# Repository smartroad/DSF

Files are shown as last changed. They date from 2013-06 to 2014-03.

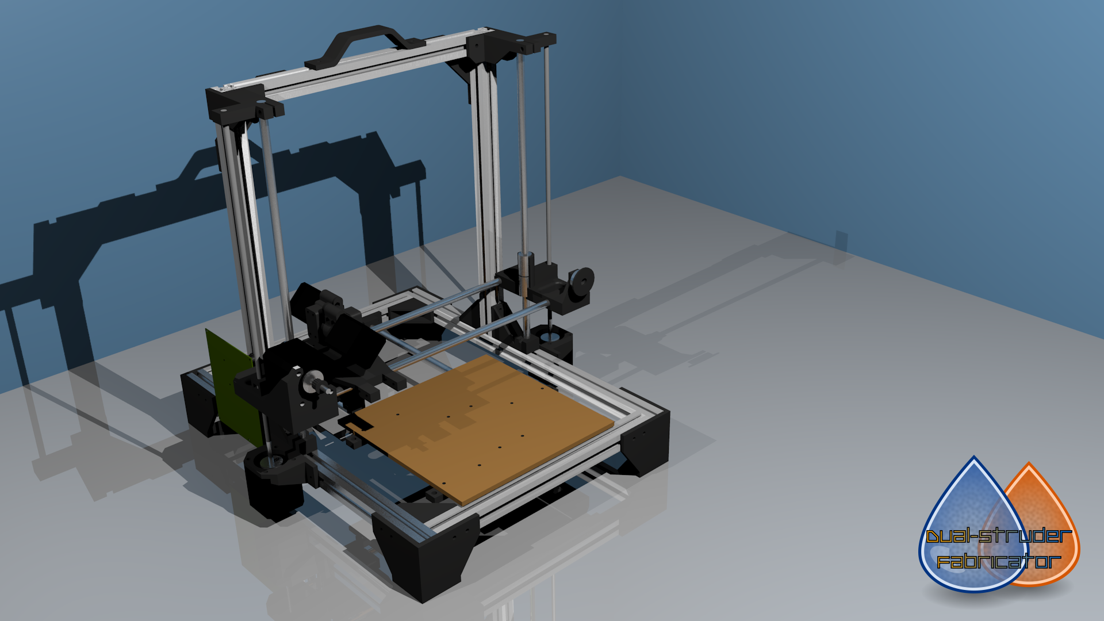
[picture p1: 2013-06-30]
Render.png

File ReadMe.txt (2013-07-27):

For some time I have wanted to design my own printer. Partly so that it will be able to do what I want and secondly for the challenge. Obviously it is much easier these days given the number of designs out there. For my design I had several things that it must be capable of:

1) More than one extruder
2) Use as many of the same vitamins as possible
3) Be simple to construct with the minimum of tools
4) Use as many printable parts as possible
5) No Bowden tube

Now I am not above thinking that some of those ideals may have to be altered but so far, in the planning stage, I think I have hit all of them.

So taking each point in turn:

It currently has space for two extruders – I wanted at least two so that I can leverage Slic3r’s ability to have one extruder for the shell and another for infill. That way I can use Faberdashery’s great colours for the shell and a cheap bulk black or white for the infill. The current extruder/hotend design means that only around 50mm of Y axis is lost when using both extruders.

Each axis uses the same linear bearings, all the printed framework attaches using M4 bolts, bearings used in the belt idlers as used in the extruders and so on. I want to not have a BoM as long as your arm and be able to order from only a few places. Personally I think this is the ideal that will change as the build progresses.

The tools that I think will be needed are screwdrivers, allen (hex) key, wire cutters and a wrench. Again this will probably change as the build progresses.

All structural support parts are printed, only the obvious items aren’t (frame, smooth rods, threaded rod etc).

No Bowden tube for the extruders are used. The current design is for a direct drive extruder – the hobbed bolt is directly attached to the stepper – which reduces the size of the extruder and the need for large printed gears. The actual reason for no Bowden tubes is purely down to I want to print flex-polyester and I haven’t been able to get it to work through my current Huxley’s Bowden. I am considering having one direct drive extruder and maybe replace the second with a Bowden system to reduce carriage weight. This would also allow for another hotend to be potentially added.

Mechanical test video is available: http://youtu.be/PYqmosbdoSI

Build log on my blog: http://fabing3d.wordpress.com/category/dsf/

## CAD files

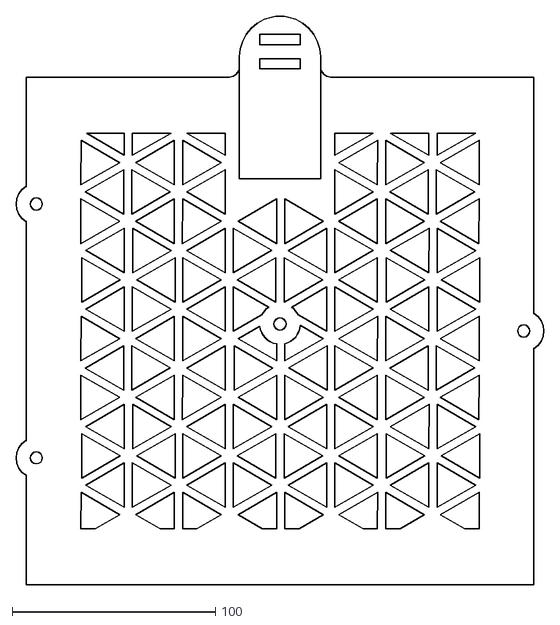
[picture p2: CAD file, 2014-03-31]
DWG/235mm Bed Carrier.dxf
260.0 x 280.0

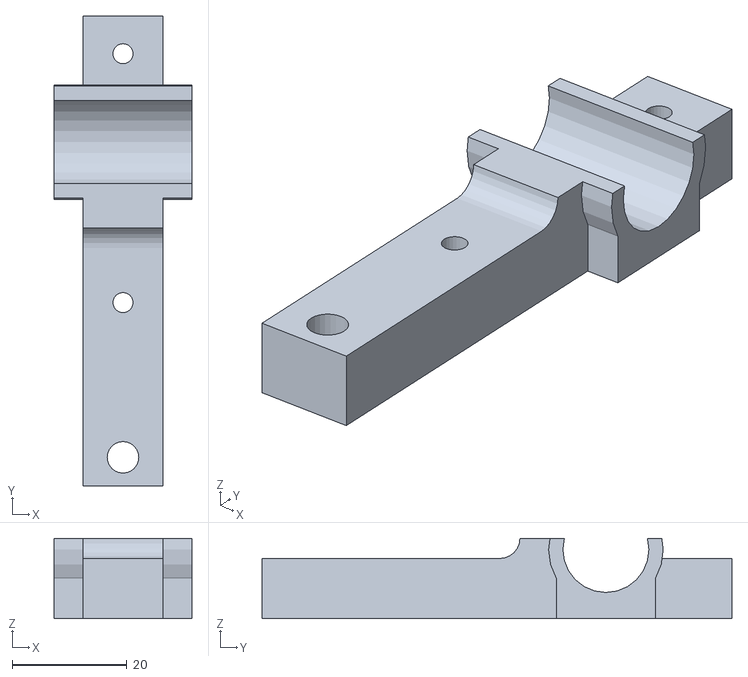
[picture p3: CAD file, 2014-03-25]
STLs/Y Axis Bed Runner Longer x3.stl
24.0 x 82.0 x 14.0

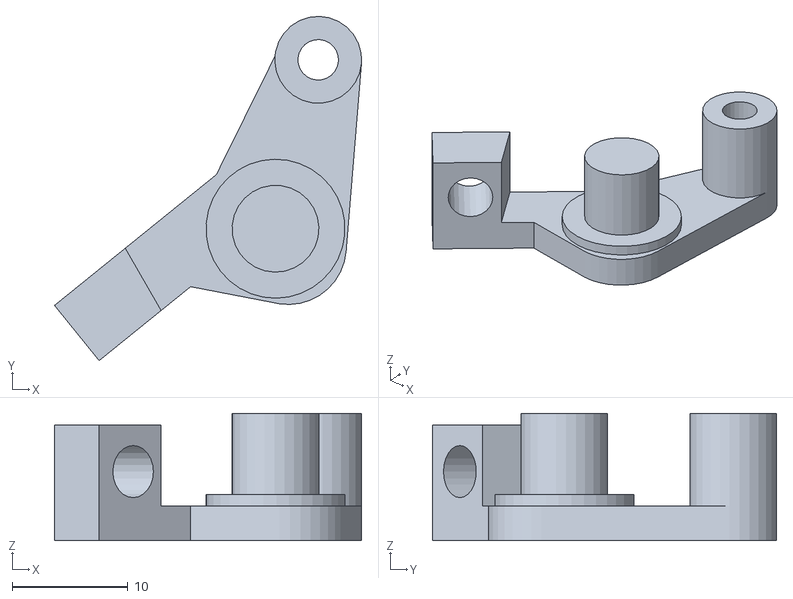
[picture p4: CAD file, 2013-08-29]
STLs/Extruder Arm.stl
26.5 x 29.7 x 11.0

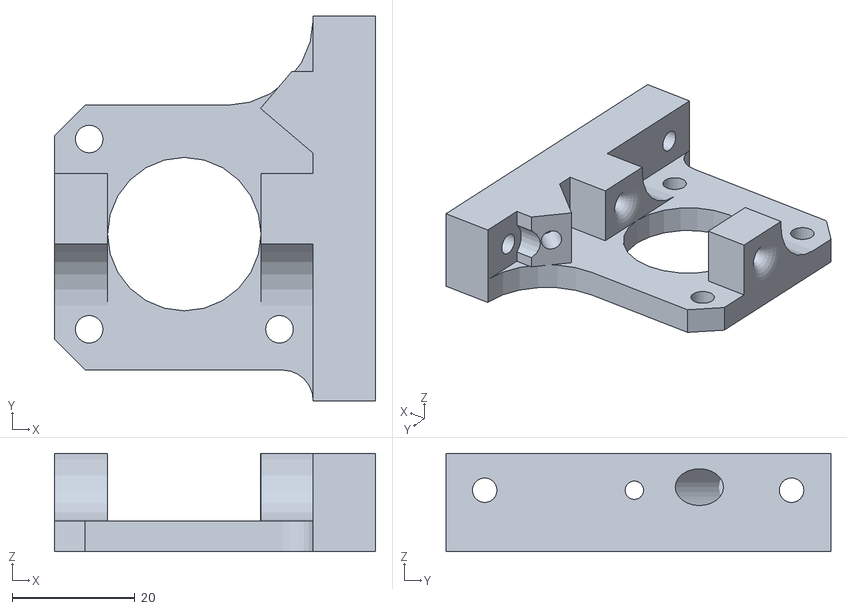
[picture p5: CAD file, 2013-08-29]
STLs/1.75mm Extruder Mount.stl
52.3 x 62.7 x 16.0

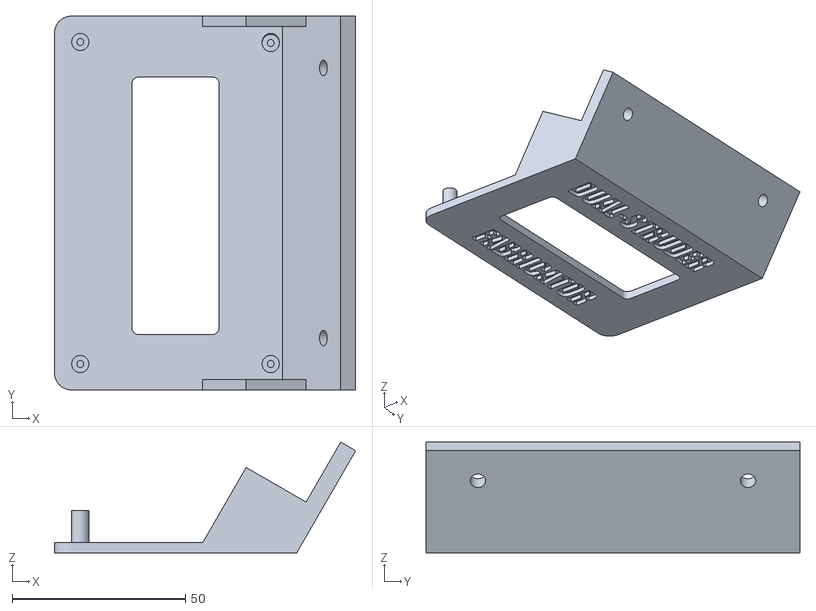
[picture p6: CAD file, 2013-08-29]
STLs/20x4 LCD Mount.stl
87.0 x 108.0 x 32.0

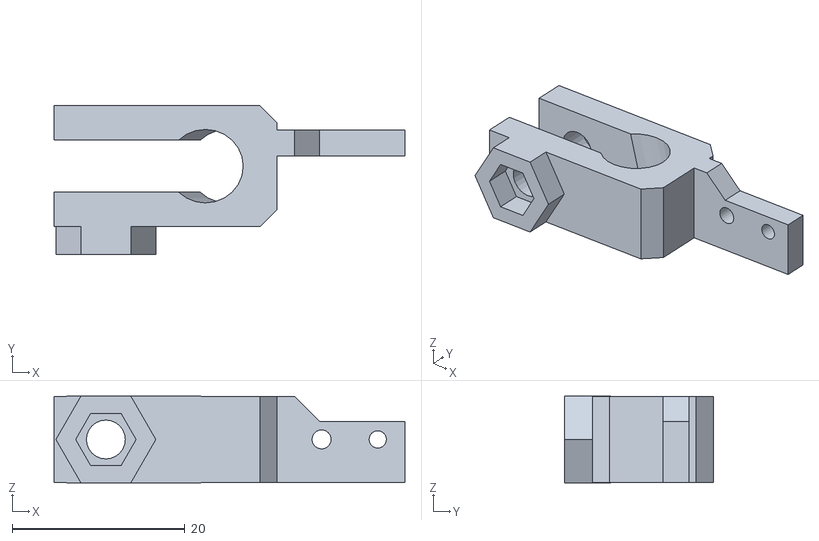
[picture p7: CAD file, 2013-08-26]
STLs/X Axis End Stop.stl
40.6 x 17.2 x 10.0

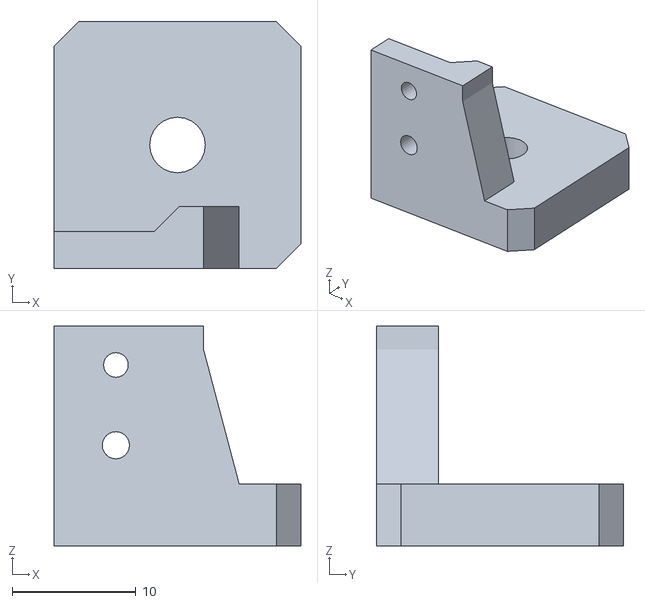
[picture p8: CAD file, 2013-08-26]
STLs/Z Axis End Stop.stl
20.0 x 20.0 x 17.8

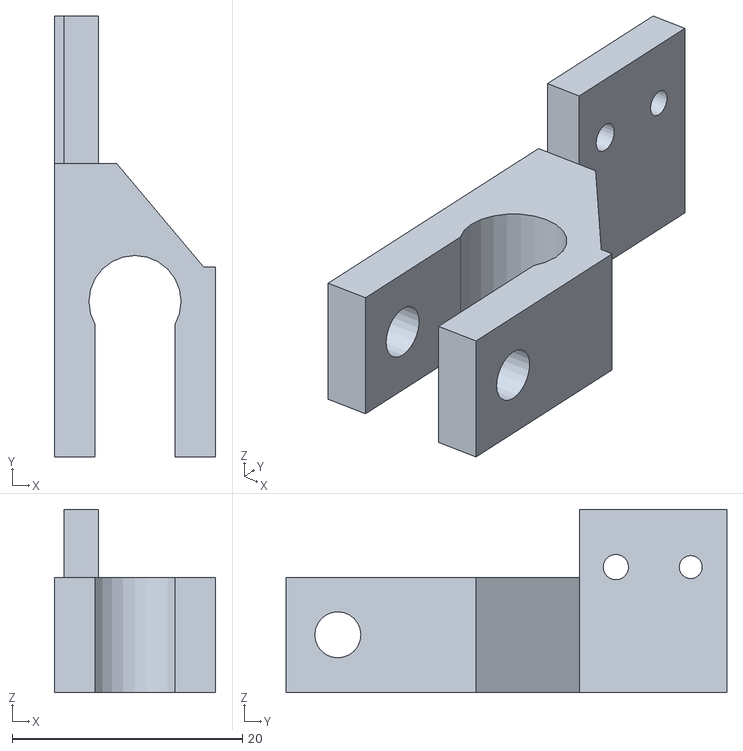
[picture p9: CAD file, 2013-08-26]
STLs/Y Axis End Stop.stl
14.0 x 38.3 x 15.9

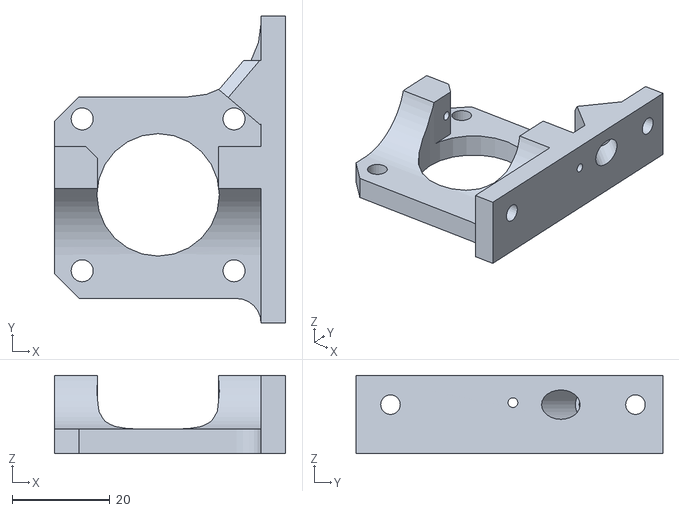
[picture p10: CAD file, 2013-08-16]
STLs/Cold End.stl
47.1 x 62.6 x 16.0

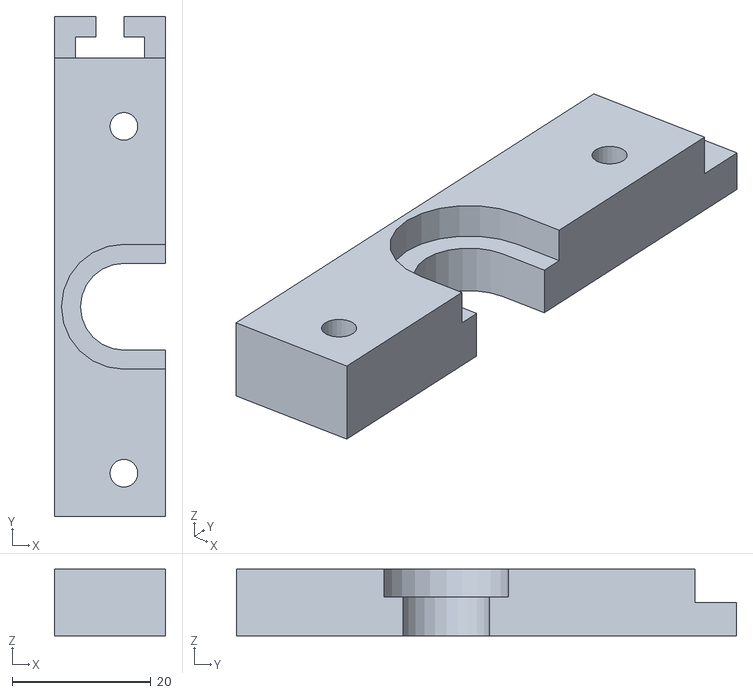
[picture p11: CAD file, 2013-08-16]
STLs/Hotend Clamp.stl
16.0 x 72.1 x 9.61

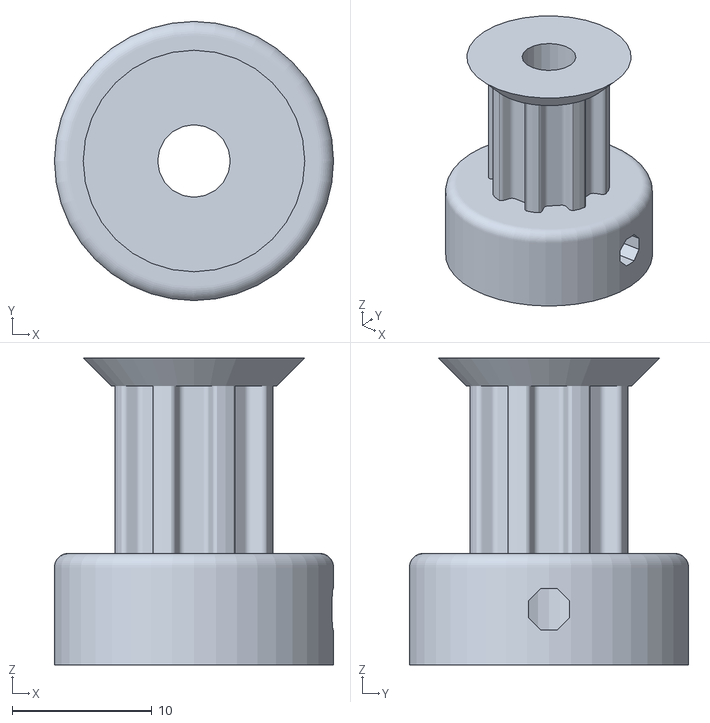
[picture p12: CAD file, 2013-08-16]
STLs/T5 Pully.stl
20.0 x 20.0 x 22.0

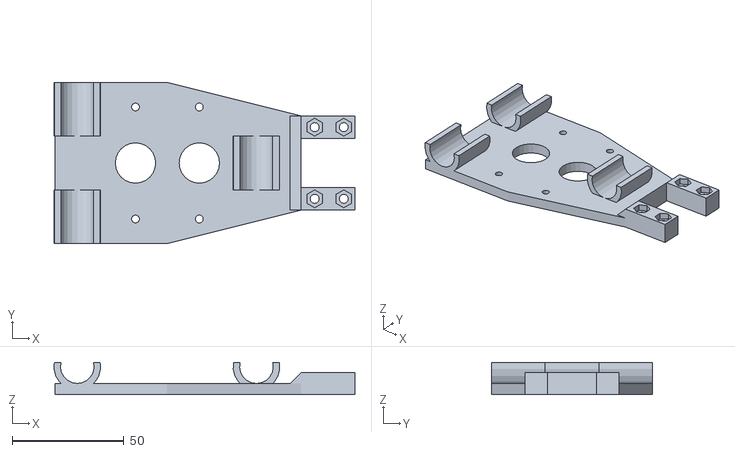
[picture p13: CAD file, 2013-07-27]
STLs/Carriage.stl
134.4 x 72.0 x 14.4

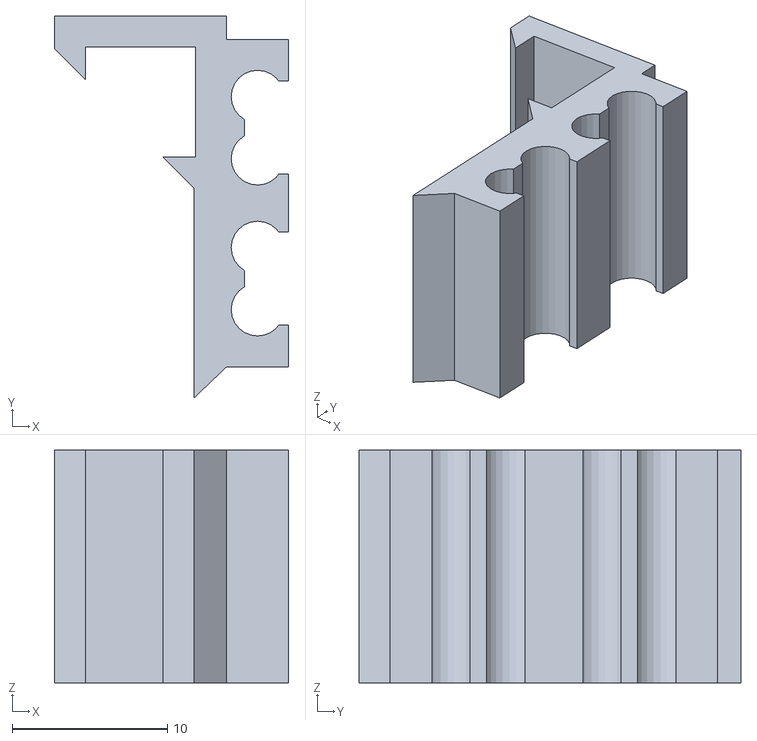
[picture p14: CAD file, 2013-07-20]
STLs/Wire Clip Qtr With Wire.stl
15.1 x 24.6 x 15.0

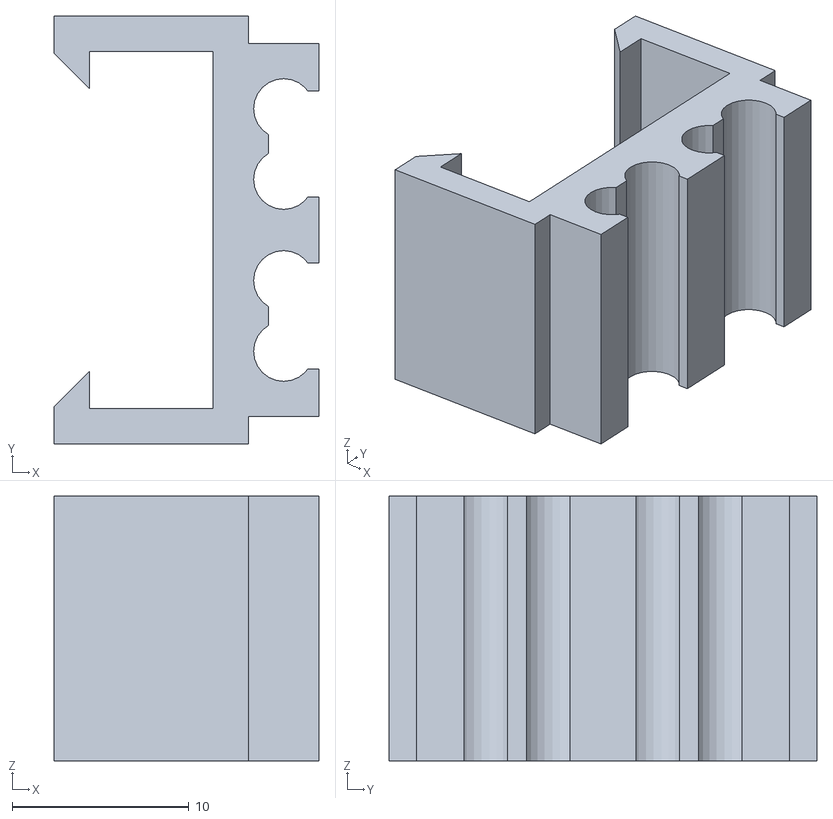
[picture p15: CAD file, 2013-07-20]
STLs/Wire Clip Half With Wire.stl
15.0 x 24.2 x 15.0

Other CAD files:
DWG/Bed Carrier.dwg
DWG/Frog.dwg
DWG/Heat Shield.dwg
STLs/Electronics Holder (Megatronics) UNTESTED DESIGN.stl
STLs/Carry Handle.stl
STLs/Frame Foot x4.stl
STLs/Frame Support Brace x2.stl
STLs/Gantry Brace x2.stl
STLs/X Axis Belt Clamp x 2.stl
STLs/X Axis Idler Cover.stl
STLs/X Axis Idler Support.stl
STLs/X Axis Motor Support.stl
STLs/Y Axis Bed Runner x3.stl
STLs/Y Axis Belt Clamp x2.stl
STLs/Y Axis Idler Holder.stl
STLs/Y Axis Motor Holder.stl
STLs/Y Axis Motor Idler Holder.stl
STLs/Y Axis Rod Holder x4.stl
STLs/Z Axis Motor Mount x2.stl
STLs/Z Axis Rod Holder x2.stl
STLs/Z Axis Upper Left Support.stl
STLs/Z Axis Upper Right Support.stl
SketchUP/Main Design.skp

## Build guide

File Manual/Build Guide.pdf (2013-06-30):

# Dual-Struder Fabricator

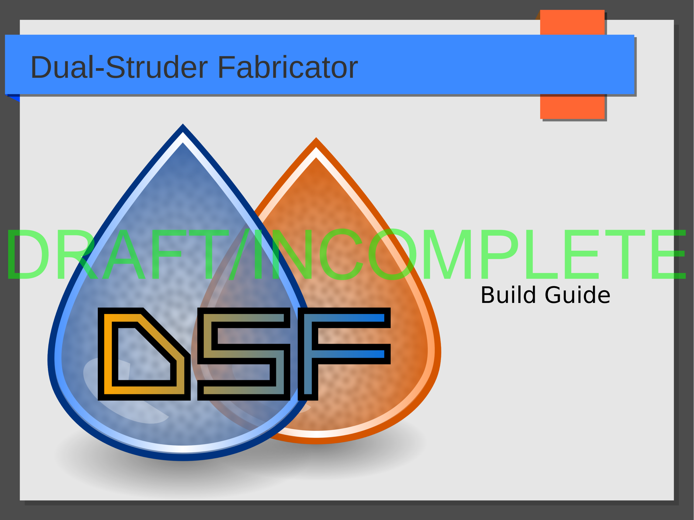
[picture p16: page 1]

# DRAFT/INCOMPLETE

# Build Guide

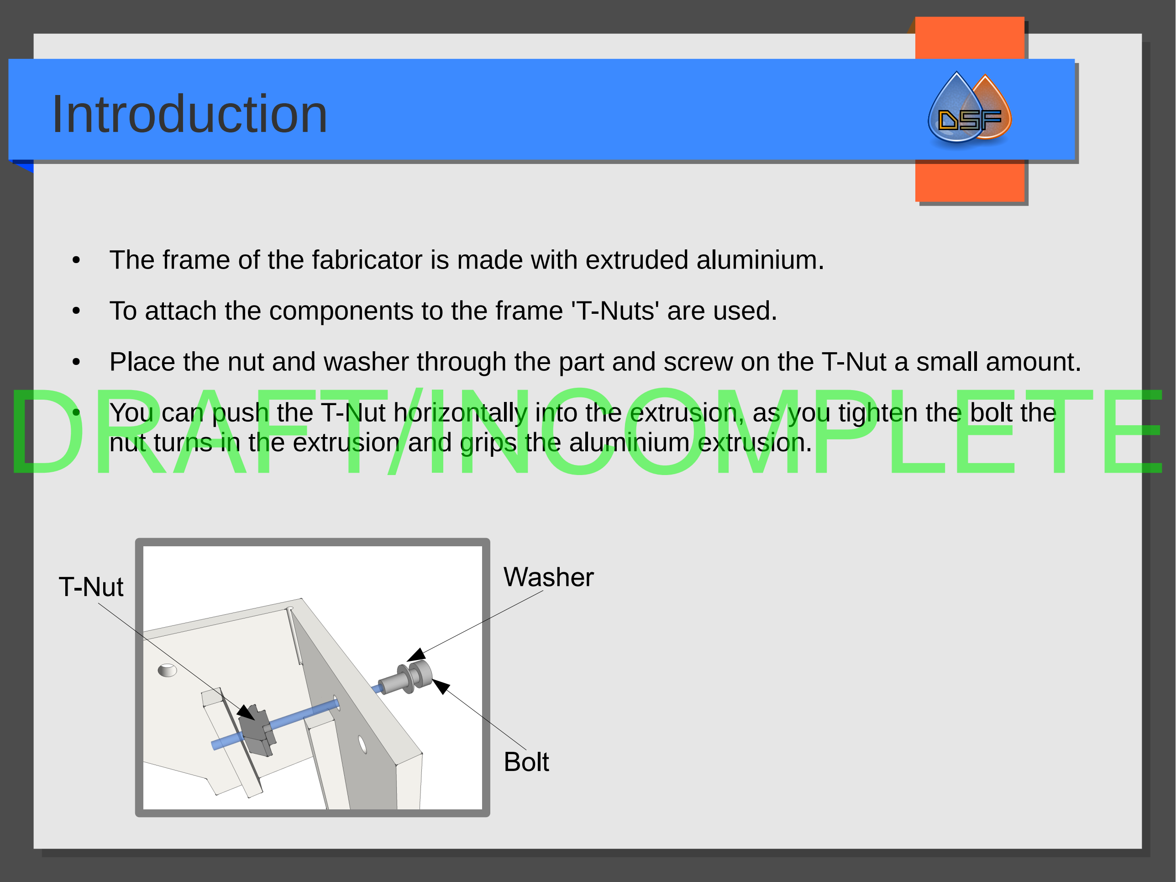
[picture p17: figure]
Introduction; T-Nut; Washer; Bolt; DRAFT/INCOMPLETE

- The frame of the fabricator is made with extruded aluminium.
- To attach the components to the frame 'T-Nuts' are used.
- Place the nut and washer through the part and screw on the T-Nut a small amount.

## - You can push the T-Nut horizontally into the extrusion, as you tighten the bolt the

nut turns in the extrusion and grips the aluminium extrusion.

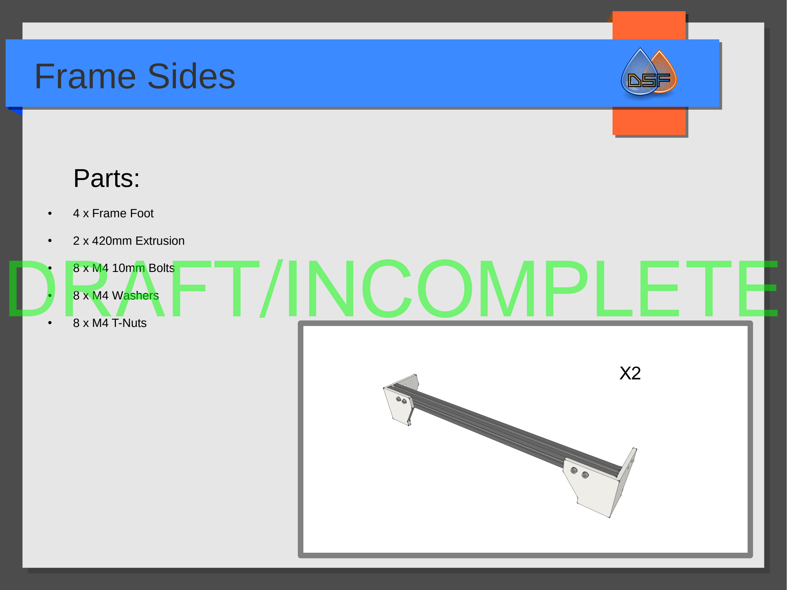
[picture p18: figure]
Frame Sides; Parts:; ● 4 x Frame Foot; ● 2 x 420mm Extrusion; ● 8 x M4 10mm Bolts; ● 8 x M4 Washers; ● 8 x M4 T-Nuts; DRAFT/INCOMPLETE

# Frame Front and Back

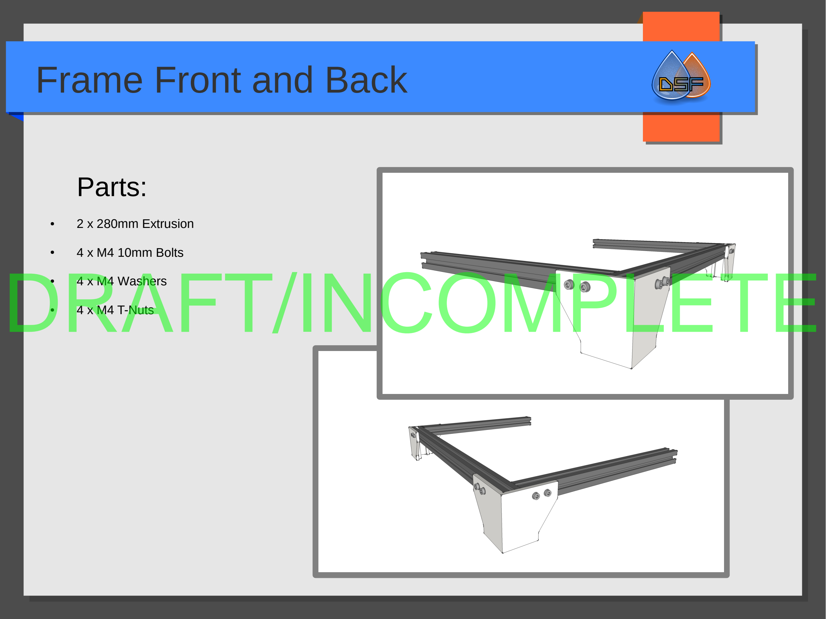
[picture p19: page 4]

# Parts:

- 2 x 280mm Extrusion
- 4 x M4 10mm Bolts
- | 4 x M4 Washers DRAFT/INCOMPLETE ● | 4 x M4 T-Nuts

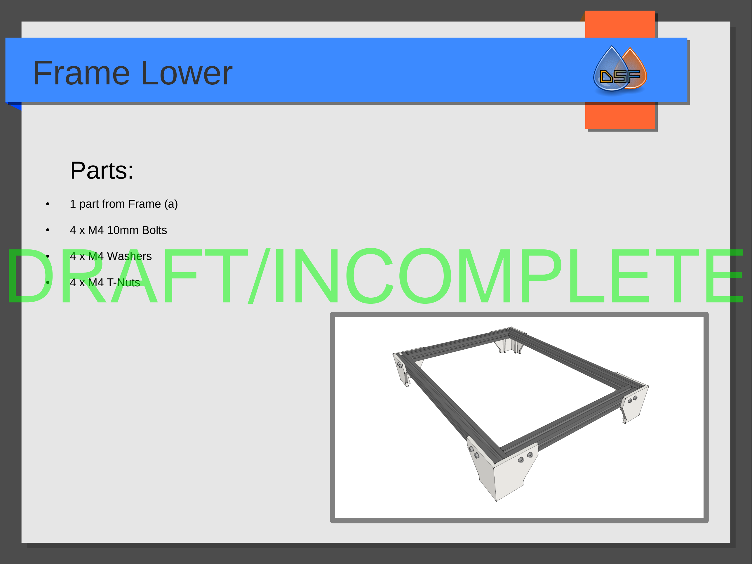
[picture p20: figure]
Frame Lower; Parts:; ● 1 part from Frame (a); ● 4 x M4 10mm Bolts

- | 4 x M4 Washers DRAFT/INCOMPLETE ● | 4 x M4 T-Nuts

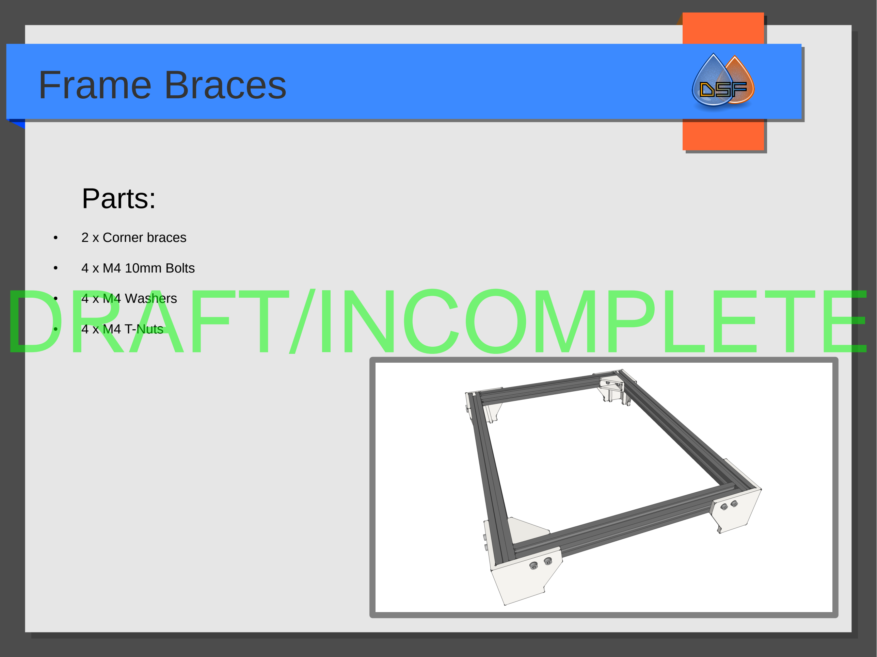
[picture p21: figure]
Frame Braces; Parts:; ● 2 x Corner braces; ● 4 x M4 10mm Bolts

- | 4 x M4 Washers DRAFT/INCOMPLETE ● | 4 x M4 T-Nuts

# Frame Gantry Uprights

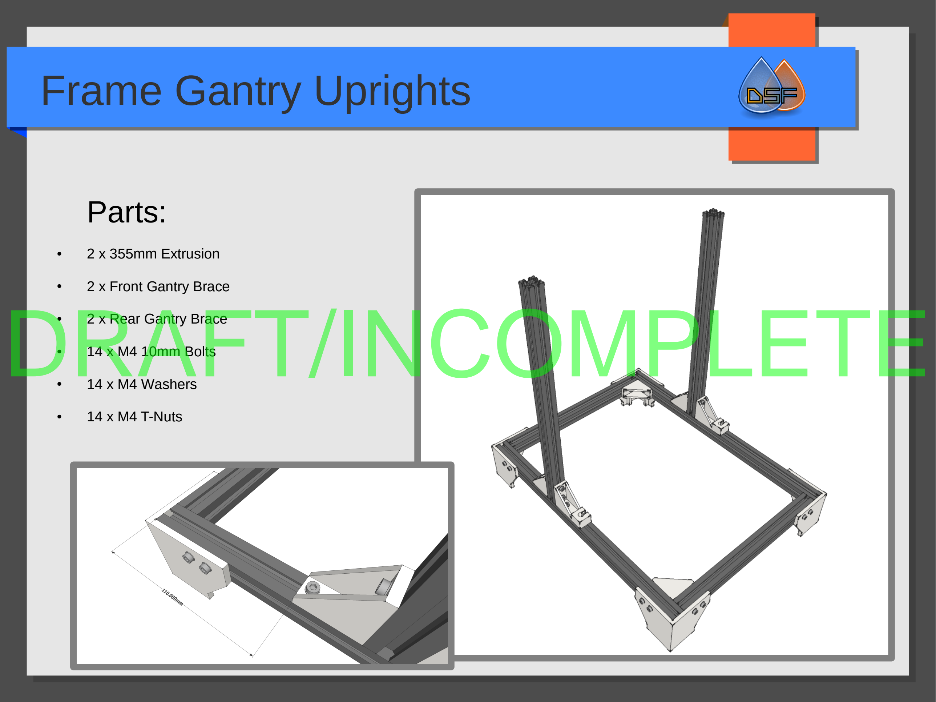
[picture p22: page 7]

# Parts:

- 2 x 355mm Extrusion
- 2 x Front Gantry Brace
- 2 x Rear Gantry Brace
- 14 x M4 10mm Bolts
- 14 x M4 Washers
- 14 x M4 T-Nuts

# DRAFT/INCOMPLETE

# Frame Gantry Top

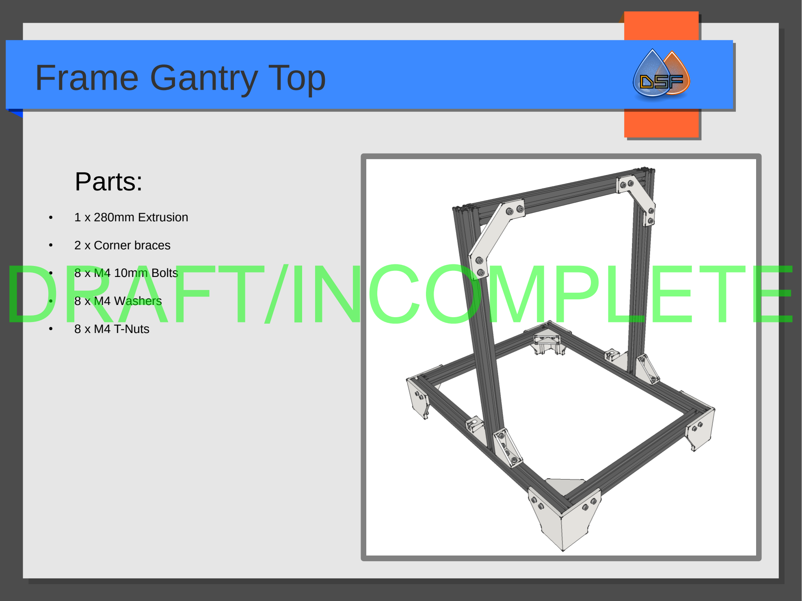
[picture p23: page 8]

# Parts:

- 1 x 280mm Extrusion
- 2 x Corner braces
- 8 x M4 10mm Bolts
- | 8 x M4 Washers DRAFT/INCOMPLETE ● | 8 x M4 T-Nuts

# Frame Gantry Z Axis Supports

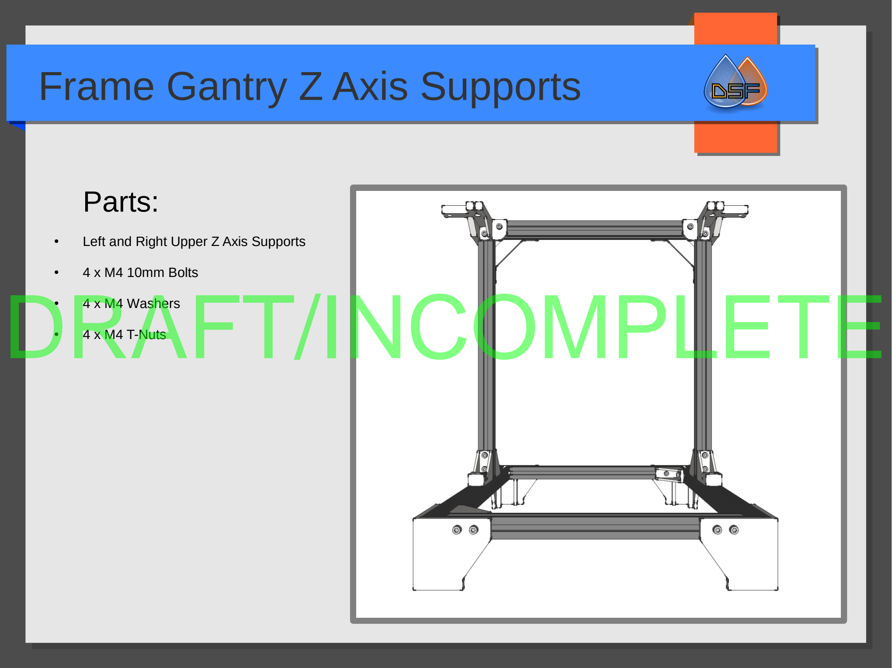
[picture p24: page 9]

# Parts:

- Left and Right Upper Z Axis Supports
- 4 x M4 10mm Bolts
- | 4 x M4 Washers DRAFT/INCOMPLETE ● | 4 x M4 T-Nuts

# Frame Handle

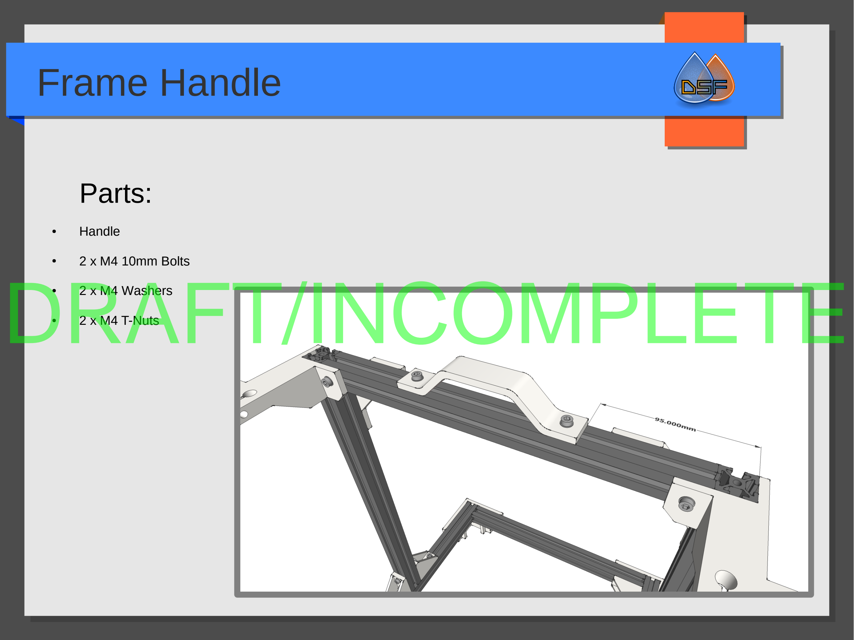
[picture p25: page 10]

# Parts:

- Handle
- 2 x M4 10mm Bolts
- | 2 x M4 Washers DRAFT/INCOMPLETE ● | 2 x M4 T-Nuts

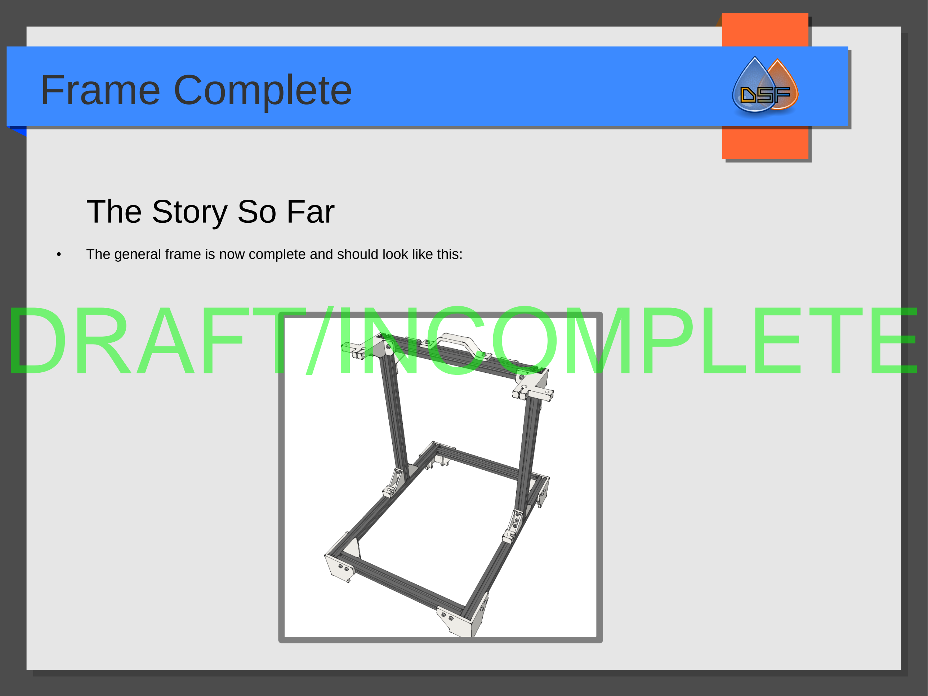
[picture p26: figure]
Frame Complete; The Story So Far DRAFT/INCOMPLETE

- The general frame is now complete and should look like this:

# Y Axis Smooth Rods

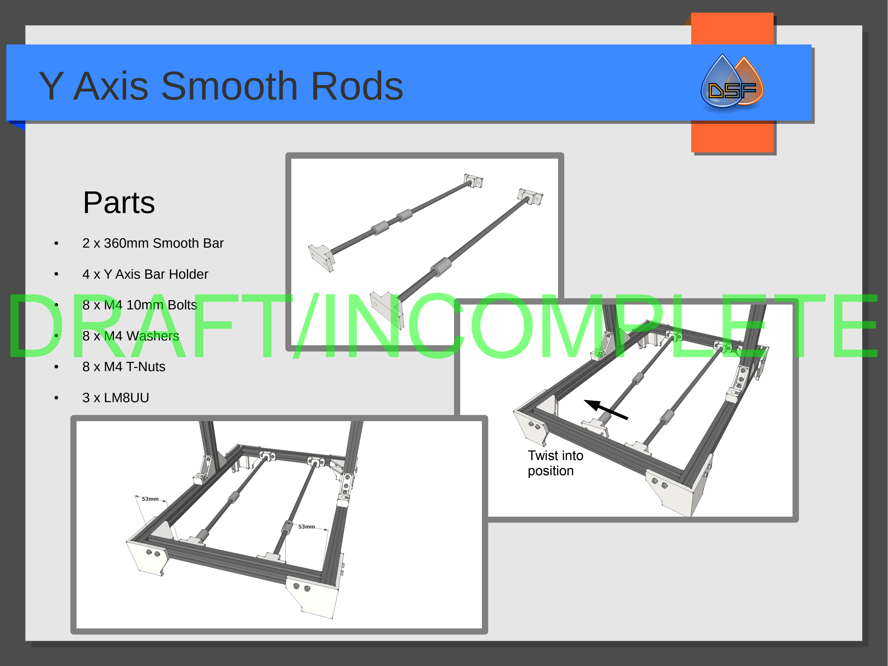
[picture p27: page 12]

# Parts

- 2 x 360mm Smooth Bar
- 4 x Y Axis Bar Holder
- 8 x M4 10mm Bolts
- 8 x M4 Washers
- 8 x M4 T-Nuts
- 3 x LM8UU

Twist into
position

# DRAFT/INCOMPLETE

# Y Axis Motor Mount and Idler

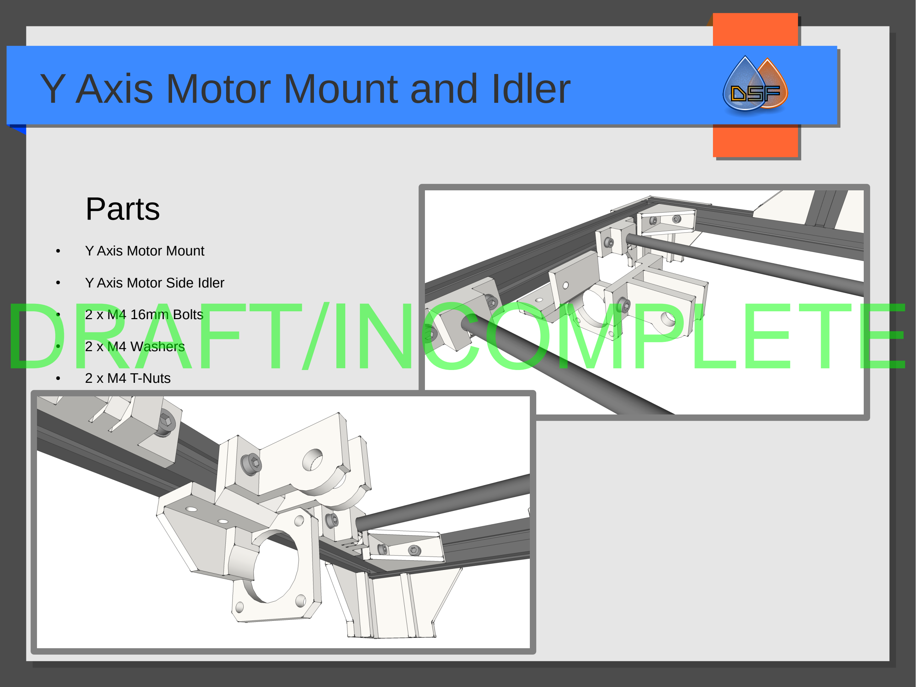
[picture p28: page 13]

# Parts

- Y Axis Motor Mount
- Y Axis Motor Side Idler
- 2 x M4 16mm Bolts
- | 2 x M4 Washers DRAFT/INCOMPLETE ● | 2 x M4 T-Nuts

# Y Axis Motor Side Idler Bearing

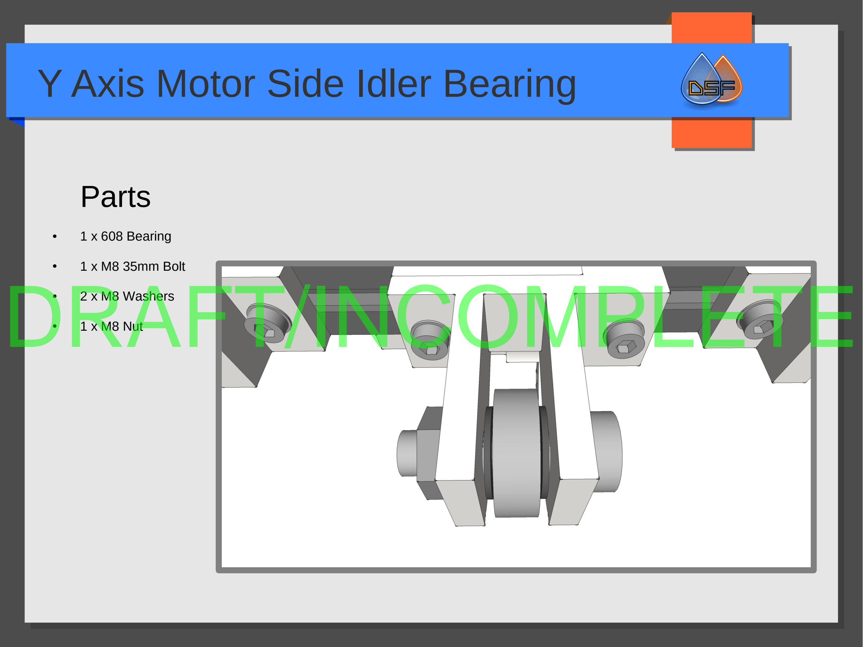
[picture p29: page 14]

# Parts

- 1 x 608 Bearing
- 1 x M8 35mm Bolt
- | 2 x M8 Washers DRAFT/INCOMPLETE ● | 1 x M8 Nut

# Y Axis Idler Bearing

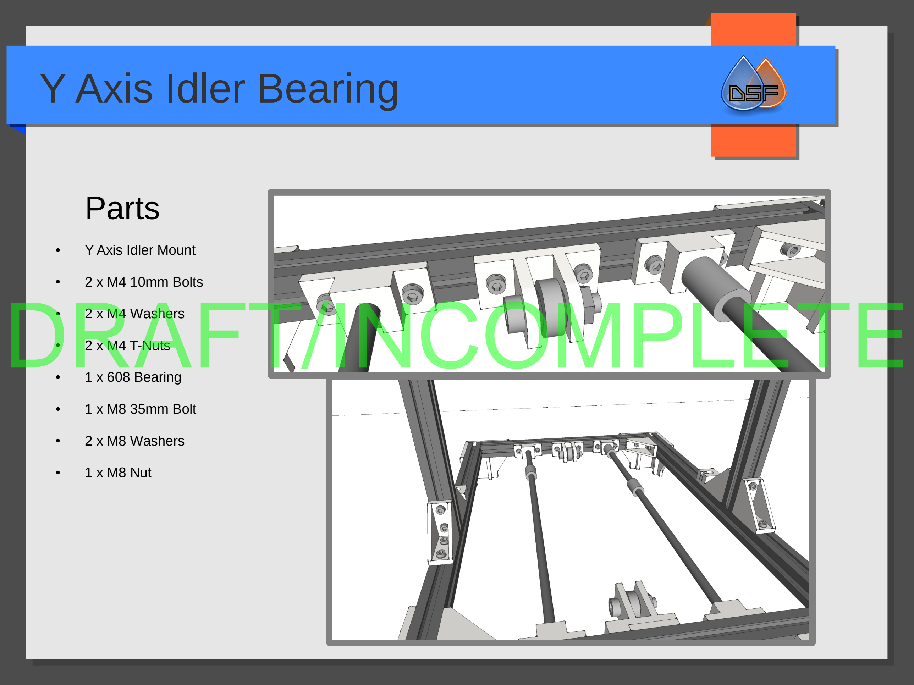
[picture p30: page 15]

# Parts

- Y Axis Idler Mount
- 2 x M4 10mm Bolts
- 2 x M4 Washers
- 2 x M4 T-Nuts
- 1 x 608 Bearing
- 1 x M8 35mm Bolt
- 2 x M8 Washers
- 1 x M8 Nut

# DRAFT/INCOMPLETE

# Y Axis Base Frog

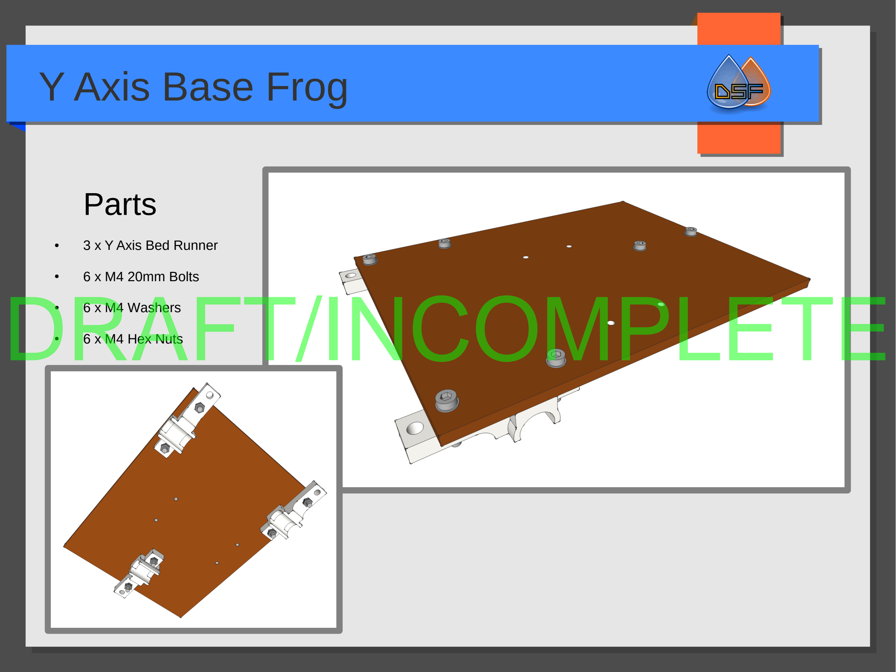
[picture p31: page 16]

# Parts

- 3 x Y Axis Bed Runner
- 6 x M4 20mm Bolts
- | 6 x M4 Washers DRAFT/INCOMPLETE ● | 6 x M4 Hex Nuts

# Y Axis Base Frog Belt Clamps

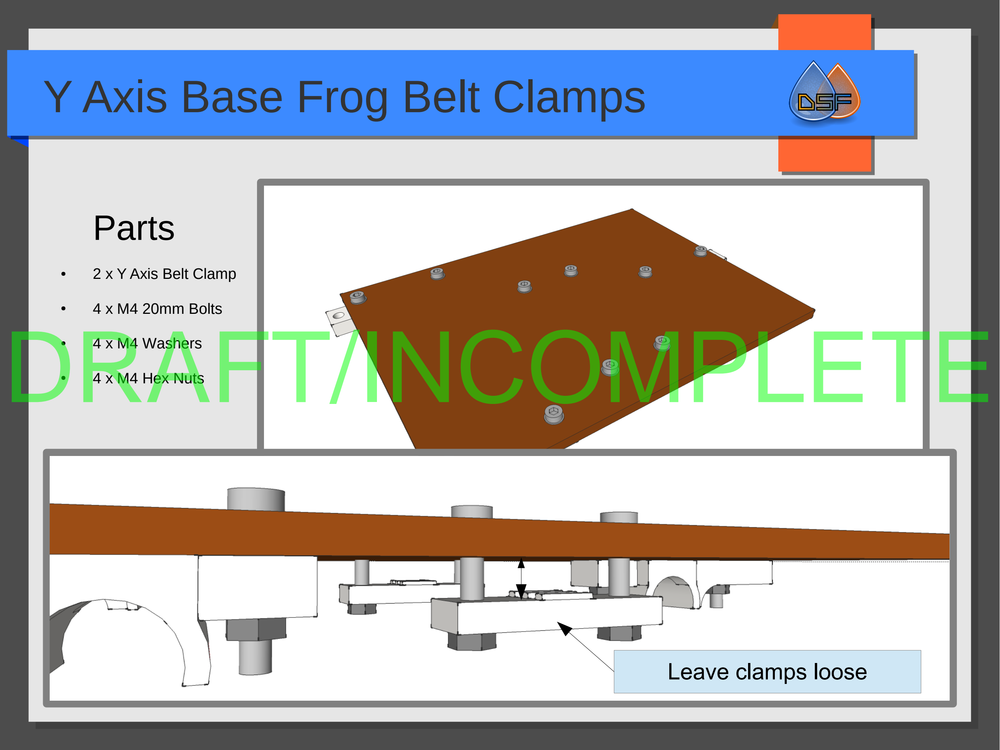
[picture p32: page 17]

# Parts

- 2 x Y Axis Belt Clamp
- 4 x M4 20mm Bolts
- 4 x M4 Washers
- 4 x M4 Hex Nuts

## Leave clamps loose

# DRAFT/INCOMPLETE

# Y Axis Base Frog Mounting

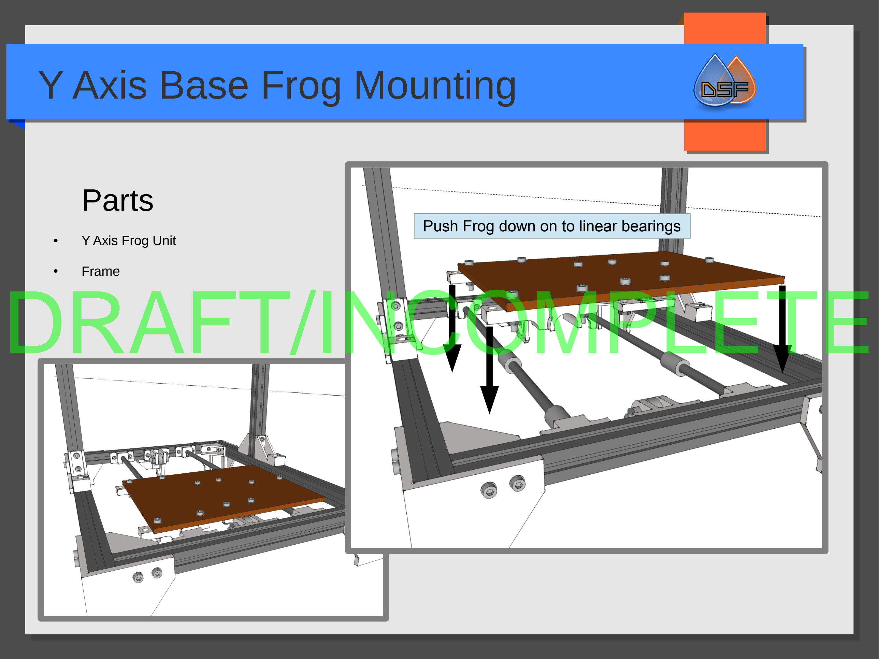
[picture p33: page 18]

# Parts

- Y Axis Frog Unit
- Frame

Push Frog down on to linear bearings

# DRAFT/INCOMPLETE

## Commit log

2013-06-30 Initial Upload
    [Carriage.stl, Carry Handle.stl, Electronics Holder (Megatronics) UNTESTED DESIGN.stl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]
2013-06-30 Reduced flange size
    Reduced the size of the flange to fit better and improve looks.
    [T5 Pully.stl]
2013-07-02 Update to Megatronivs V2 Holder
    Modified thickness at bolt points to improve fitting
    [Electronics Holder (Megatronics) UNTESTED DESIGN.stl, Main Design.skp]
2013-07-02 Added more depth to holder
    More depth needed to allow for bolt head height, was shorting on pins
    underside PCB
    [Electronics Holder (Megatronics) UNTESTED DESIGN.stl, Main Design.skp]
2013-07-07 New end stops
    New end stops holders uploaded for the axis using the microswitch from
    RS Electronics: 682-1547
    [X and Z End Stop x2.stl, Y Axis End Stop.stl]
2013-07-07 Clips to retain wires in extrusion
    [Wire Clip Half.stl, Wire Clip Qtr.stl]
2013-07-20 Wire clips with wire main power supports
    These clips help to not only keep the wires in the extrusion but also
    have clips on the back to allow the PSU cables to be routed neatly.
    [Wire Clip Half With Wire.stl, Wire Clip Half.stl, Wire Clip Qtr With Wire.stl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]
2013-07-27 Y Axis Laser Cut Parts
    [Frog.dwg, Heat Shield.dwg]
2013-07-27 Updated Carriage
2013-07-27 Altered Clamps and mounts for new coldend
    The clamps for the belt have been moved to the top of the carriage
    rather than the sides to make it easier to attach. Mounting holes moved
    ready for new coldend.
    [Carriage.stl]
2013-08-16 Updates and LCD holder
    [16x2 LCD Mount.stl, T5 Pully.stl]
2013-08-16 Extruder Parts
    [Cold End.stl, Extruder Clamp.stl]
2013-08-26 New Endstops
    Adjustments to make endstops more ridged
    [X End Stop.stl, X and Z End Stop x2.stl, Y Axis End Stop.stl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]
2013-08-26 Update to X Axis Endstop
    Previous wasn't level or named correctly
    [X Axis End Stop.stl, X End Stop.stl]
2013-08-29 New 20x4 LCD Holder - Update to SketchUP file
    [16x2 LCD Mount.stl, 20x4 LCD Mount.stl]
2013-08-29 Extruder Mount
    [1.75mm Extruder Mount.stl]
2013-08-29 Rename and Extruder Arm
    [Extruder Arm.stl, Hotend Clamp.stl]
2014-03-13 Larger Bed Carrier
    [Bed Carrier.dwg, Bed Carrier.dxf]
2014-03-25 Larger Bed Carrier
    New parts to increase bed size to 235x235mm
    [235mm Bed Carrier.dxf, Bed Carrier.dxf, Y Axis Bed Runner Longer x3.stl]
2014-03-31 Fix Dimensions
    [235mm Bed Carrier.dxf]
